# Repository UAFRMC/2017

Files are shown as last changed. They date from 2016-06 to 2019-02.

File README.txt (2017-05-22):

This is the public repo for UAF's NASA Robot Mining Contest team,
Aurora Robotics.
This is the firmware and control stack for UAF's entry in the NASA Robot Mining Competition.

Public access:
	git clone https://github.com/UAFRMC/2017

Ask Mike or Dr. Lawlor to get write access!

2017 Competition
KSCCOMM-GUEST wifi: 1632061632051282171927740A

------------- 2015 notes:
Laptop battery power check:
	cat /sys/class/power_supply/BATX/charge_*
The first two are charge values for full; the last is current charge.

As-built storage bucket dimensions:
  17.75 inch * 17 inch * 3.5 inch = 17.3 liters -> 17Kg at 1 Kg/L density (fluffed)

---------- 2014 notes:
New 2014-05 board:

Power plug:
  tx1 via opto-isolator: orange/white
  a8: orange, not connected (avoid noise on opto line)
  a9: blue, mine voltage
  a10: green, spare input
  a11: brown, 24v bus
  brown/white: motor side ground

Front plug:
  53/A15: blue, front wheel right encoder
  52: orange, (5v) encoder supply
  51: spare button input
  50/A14: green, front wheel left encoder (optional)
  White: all grounds

Back/bucket plug:
  49: orange, (5v) encoder supply
  48: orange/white, spare input
  47: green, back right button
  46/A13: blue back bucket
  45: brown/white, spare
  44: brown & blue/white, back left button 
  43: spare input

Infrared board: pink RJ45 wires
A5	A1	orange/white: read side of mining detector
   5		orange: 5V feed for ALL ir detectors (soft power for both)

A6	A2	green/white: ir detector, bin-full
3	A4	green: LED, bin-full

4	7	blue: LED, bin-half-full
A7	A3	blue/white: ir detector, bin-half-full
	
 hardwired	brown/white: LED ground (COMMON ground, hardwired)
2	6	brown: LED for mining encoder

Wiring hookup: 
mining:  brown brown/white LED    orange orange/white detector
full:	green  brown/white LED    orange green/white detector
half:   blue   brown/white LED    orange blue/white detector

Actuator Ecoder wires:
Yellow: High
White: GND
Purple: Signal

Linear actuator to RJ45 wiring:
	yellow: 5V for potentiometer position encoder, orange on RJ-45.
	white: ground for potentiometer, white/blue on RJ-45.
	purple: potentiometer output, blue or green on RJ-45.
	red: motor+, either brown (front) or separate wires (bucket)
	black: motor-, either white/brown or separate wires

# Add backend and viewer directories to path
AURORA=/home/robot/robotmining/autonomy
PATH="$AURORA/aruco/viewer:$AURORA/backend:$PATH"
export PATH

-------------
OLD 2014-03 board:

OLD: Internal voltage monitoring: 2014-03 board (OLD)
	A8: orange battery 12V bus
	A9: battery ground (drive sabertooth)
	A10: brown battery 24V bus
		Weirdly, it reads about 3VDC lower than reality, possibly due to some sort of current backfeed in the voltage divider.
		Battery sags by about 15DN under a 10A load.
	A11: battery ground (mine sabertooth)
	A12: green mining motor voltage
		Typical run voltage is 10-13DN less than battery.
		Stall voltage is 20-22DN less than battery.
		Firmware calls it "stalled" with >18DN difference.
		Swaping to a CAT5 cable, still about 10DN run, but 30+DN stall.
	
OLD: External switches:
	44- left bumper switch (brown & white/green ground)
	47- right bumper switch (green & white/green ground)

OLD: Dump actuator potentiometer hookup:
	49-orange (5V) & white/blue (gnd)
	46 - blue - analog out for dump potentiometer (jumpered to A0 for now)

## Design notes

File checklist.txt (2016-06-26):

A: away team    B: bridge

============================================================
Startup
============================================================
(A) Router Plug-in
	(B) Pilot has IP
(A) Marker Setup
(A) Align Hooks
(A) Battery Reset
(A) Arduino Cable
(A) Laptop Open
(A) Safety Off
(A) Onboard Network
	(B) SSH
	(B) Start backend
	(B) Telemetry
	(B) Drive mode
(A)//Webcam Focus
(A)//Webcam Direction
(A) Close Laptop

============================================================
End
============================================================
(A)Safety On
(A)Run "off"
(A)Wh Reading
(A)Battery Unplug
(A)Cleanup

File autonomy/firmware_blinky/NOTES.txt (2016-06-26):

Stepper + blinky receiver
2mm gap blinder black PLA
Arduino nano emitter & detector

Stepper safe zone is about 100 to 3850.

Taking individual jumps of size 100 gives a cycle time of 30 seconds (!), way too slow.  And we seem to miss IR pulses during the jump.
Taking steps of size 10 takes over a minute per cycle.

Multipath via big shiny objects like laptop screen is definitely a thing.

Overriding AccelStepper::step and adding an IR probe seems to work well.  That nest of virtual functions is not at all high performance anyway.

Blasting out one 8-bit message with a delay of 1ms is about one message every 3-4 steps.
With the wide 2mm blinder gap, message receive window seems to be about 30-40 steps, so we get about 10 messages.

Backlash is big--average received step is:
	1450-3 on downhill
	1488-90 on uphill
	Average shift is 33.8 steps, so split difference at 17 steps in each direction.
Standard deviation is 2.3 or 1.6 (down)
Worst case over 500 runs is +-5 (!).

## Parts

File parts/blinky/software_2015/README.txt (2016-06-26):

Simple infrared blinking beacon.  Blink rate is fairly slow, 4 or 5 milliseconds per cycle, to allow software signal processing.

Signal recovery is using a complex-valued "phasor" system, where we scale the incoming amplitude by a time-varying complex helix.  Frequencies that don't match the helix spin rate have low resulting amplitudes.

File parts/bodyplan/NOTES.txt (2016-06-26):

Robot driving coordinate system:
X: robot's left and right, robot right +x
Y: robot's forward and backward, robot forward +y
Z: robot's up and down, up +z

Fabrication coordinate system:
Y=0 is back of bottom steel tubing

Gearboxes:
	Diameter 9cm at output gear
	Total height 10.5cm
	axle to motor max: 10.5cm

Bottom frame:
	Y=0 is back end of tube
	Y=2.25 inch is axle pivot hole
	Y=4.75 inch is start of back drive motor mount
	Y=7.125 is start of back electronics box upright 
		21.75" tall
	Y=15.5 is centerline of ski mount
	  total of   2.875" between inner holes
	  total of   4.5" between outer holes
	  ski mount is 6 inches long

	Y=18.5 is start of up/down linear mount
		1.5" tall to pivot point
	Y=22.75 is start of front electronics box upright
	Y=25.25 is start of front drive motor mount
	Y=29.125 is front end of tube

Mining head:
	Back support is at 45 degrees to vertical in neutral configuration (linear actuators at 12" center to center)
		Back pivot to mining head is 19"
		Back pivot to linears is 20"
	Mining head is at 60 degrees to vertical in neutral
		From bottom of mount:
		Runs 5.25" up to mine drive axle
		Runs 19.25" down to mine idler axle

Linear actuators: max length 16" axle to axle

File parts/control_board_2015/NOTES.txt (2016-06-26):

Idea is the thing sits on the end of the Arduino Mega, occupying analog A8-15 (for battery & motor voltage monitoring) and the last few digital pins.

For monitoring voltages up to 24.8VDC from a 4.5V microcontroller, I need a voltage divider to ground.  I have a bunch of big 2Kohm and 348ohm surface mount resistors, which would give me up to 25.8VDC monitoring capability, while burning only 10mA of static current.  These surface mounts are only 3mm/0.11" wide, so they should be easy to fit.

2014-03-01: Milled prototype board, and soldered it up.

I needed to hack in "pinMode(p,INPUT_PULLUP)" support for Firmata (hardcoded, but seems to basically work).  Weirdly, you can't seem to digitalWrite in INPUT_PULLUP mode.

For the encoder wheel, the blue/green lines show up as digital pins 53 and 50.
The orange/brown lines should thus be digital pins 51 and 52.

It's tempting to switch the analog inputs over to RJ-45, like the digitals.

Analog via 2K:
	- Vin 132
	- Gnd 0
	- 3.3v rail 97-103 (implying total range is about 33v)
	- Aref 149-150
The Mega can call analogReference(INTERNAL1V1) for a 1.1v internally generated reference (and hence better millivolt accuracy).

-----------------------------
Version 2:

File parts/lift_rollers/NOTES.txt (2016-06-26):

Storage bag lifting rollers, with drive splines to attach to mining head crossbar.

Mining head crossbar is 1.5 inch (nom) ABS pipe OD: 48.5mm

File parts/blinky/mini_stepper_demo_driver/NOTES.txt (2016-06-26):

http://smile.amazon.com/USPRO-Stepper-28BYJ-48-4-Phase-ULN2003/dp/B00JB22IQC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

http://www.bajdi.com/joystick-and-2-28ybj-48-stepper-motors/

Each coil is about 100mA draw, for 200mA total.
64 steps per internal revolution, but it's geared way down, 
to approximately 2048 steps per output revolution.

CAD dimensions:
Output shaft:
	4.91mm dia
	2.91mm between flats
	5.9mm flat height
	8.24mm tip to boss start

Output boss:
	9.15mm diameter cylinder
	1.1mm boss height above face
	1.35mm from boss rim to body rim
	-> 8.12mm from body center to boss center

Body:
	28.1mm body diameter
	19.3mm body height
	18.1mm back wiremount width
	3.1mm back wiremount additional radius
	-> 17.15mm wiremount back radius

Mount:
	4.11mm dia mounting ear holes
	7mm dia outside ears
	41.91mm outside to outside ear
	30.81mm inside to inside ear
	-> 17.45mm body center to ear center

To find the actual steps per rev, hot glued a mirror to the output shaft, and bounced a laser off it.  There's a ton of backlash.  Every 4th half-step doesn't shift the output position.

2037 steps/rev?

Align at:
1
2038
4074
6112
8149-50
10187
12228

Dropped maxsteps from 4K to 2K:
1
2038
4080
6116

Dropped accel to 50:
1
2039
4077
6114
8149
10187
12223
(lost steps on return)

Dropped maxsteps from 2K to 1K:
1
2039
4074
6112
8150
10189
12227
(STILL loses steps on return!)

Dropped maxsteps from 1K to 600:
0
2038
4076

8156

12233
back to 0 OK.

Backlash is equivalent to about 20 steps.

http://forum.arduino.cc/index.php?topic=71964.15
Counted teeth in gearbox to get
25792/405 = 63.68395
25792/405*32 =  2037.88641975309

12227/6 =  2037.83333

http://www.airspayce.com/mikem/arduino/AccelStepper/
http://www.embedded.com/design/mcus-processors-and-socs/4006438/Generate-stepper-motor-speed-profiles-in-real-time

---------------
Plugged directly down into Arduino Uno's pins 8-11, the appropriate startup is:
AccelStepper stepper(AccelStepper::HALF4WIRE, 8,10,9,11);

Driven from 12V (lithium 3S), the stepper gets wickedly hot (approx 140F), and draws half an amp, but this works reliably:
     stepper.setMaxSpeed(3000.0);  stepper.setAcceleration(100000.0);

Driven from 8V (lithium 2S), draw is 0.3 amp, and the stepper only hits 110F (toasty).
     stepper.setMaxSpeed(3000.0);  stepper.setAcceleration(100000.0);

On a 5Ah lipo, running at 8V for an hour only drops the lipo by 0.2V (maybe 10% of full charge).

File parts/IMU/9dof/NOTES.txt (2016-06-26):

9DOF sensor board: 
https://www.sparkfun.com/products/10724

Code to pull I2C data:
http://playground.arduino.cc//Main/SEN-10724

Typical values:
A	49	-5	233	G	97	171	45	C	-24	-306	-9
A	41	-9	234	G	102	180	62	C	-24	-306	-9
A	41	-9	234	G	119	178	43	C	-24	-306	-9
A	47	-3	245	G	127	186	71	C	-24	-306	-9
A	55	-6	247	G	126	150	57	C	-24	-306	-9
A	55	-6	247	G	93	171	77	C	-24	-306	-9
A	48	-8	240	G	122	170	62	C	-24	-306	-9
A	47	-2	249	G	103	199	63	C	-24	-306	-9
A	52	-2	228	G	110	183	53	C	-24	-305	-9
A	52	-2	228	G	87	128	66	C	-24	-305	-9
A	52	3	246	G	102	170	68	C	-24	-305	-9
A	42	-17	229	G	110	178	48	C	-24	-305	-9
A	42	-17	229	G	109	186	75	C	-24	-305	-9
A	45	-7	243	G	120	175	66	C	-24	-305	-9
A	49	-4	245	G	86	167	57	C	-24	-305	-9
A	49	-4	245	G	109	174	67	C	-24	-305	-9
A	47	-1	239	G	107	155	61	C	-24	-305	-9
A	44	-3	239	G	93	168	56	C	-24	-305	-9
A	44	-3	239	G	105	196	80	C	-23	-304	-9
A	54	-2	247	G	104	152	72	C	-23	-304	-9
A	51	2	254	G	104	180	62	C	-23	-304	-9
A	51	2	254	G	73	163	48	C	-23	-304	-9
A	52	0	249	G	83	153	62	C	-23	-304	-9
A	52	-4	245	G	115	153	83	C	-23	-304	-9
A	52	-4	245	G	66	151	30	C	-23	-304	-9
A	44	-13	238	G	97	164	15	C	-23	-304	-9
A	49	-4	241	G	111	190	66	C	-23	-304	-9
A	49	-4	241	G	93	178	69	C	-23	-304	-9
A	55	-12	235	G	97	178	69	C	-23	-305	-9
A	51	0	249	G	81	155	63	C	-23	-305	-9

Accelerometer: ADXL345
Accelerometer G value shows 267 dn == 1 g.  Vector points down. 
	Datasheet rating is 4 milliG / LSB; scale factor is per chip.
Accel X axis seems the opposite of what's shown on the board, unless you flip it in software (fixed).
Accelerometer values are horribly ratty, and bounce around a ton even if you average 100.

Gryo: ITG-3200
Gyro readings seem to be relative: rates, not angles.
Gyro outputs are *very* clean, detecting even very slow rotations.
	Datasheet rating is 14 LSB per degree per second (!), up to 2000 degrees/sec.
	Datasheet sample rate is 1-8kHz.
It also reads temperature as a 16-bit quantity.
Gyro zero drift is about:
	97	60	50
Sadly, the drift slowly drifts.  The next day:
	-95.71	-114.18	42.21

Three I2C transactions results in a sample rate of about 300Hz.

Long-term averaging shows standard deviation of each reading is around 1 LSB.
1.1 1.1 1.4	1.3 1.9 1.3	0.23 0.27 0.24
Magnetometer is tighter, 0.23-0.27LSB.

Magnetometer output is funky.
We can't use a magnetometer for NASA anyway.

Same chips, better axis layout, but no magnetometer, $40:
	https://www.sparkfun.com/products/10121

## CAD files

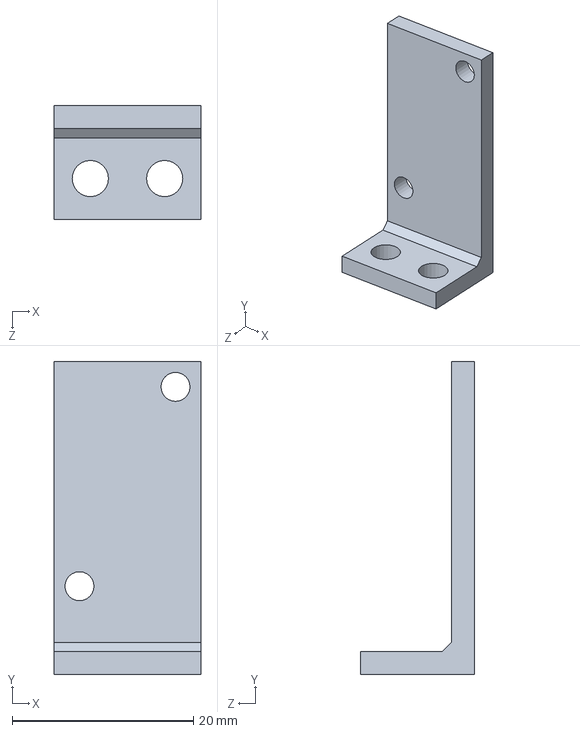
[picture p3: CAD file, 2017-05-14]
parts/limit_switches/switch_L_bracket_left.SLDPRT
16.2 x 34.5 x 12.5 mm

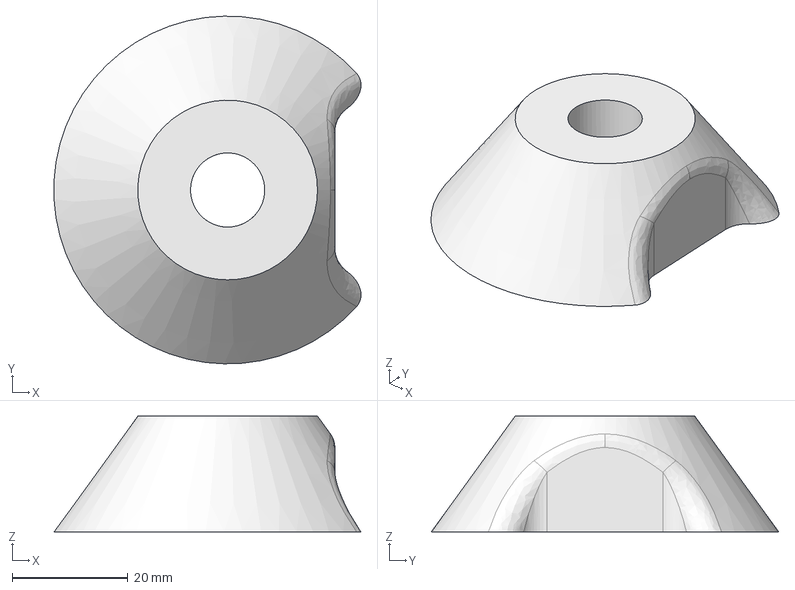
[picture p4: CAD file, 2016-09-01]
parts/mantis_2015/centercone_v2.FCStd
53.0 x 60.0 x 20.0 mm

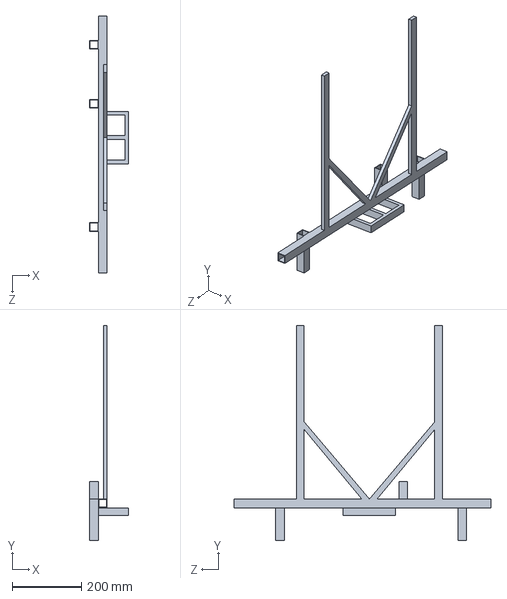
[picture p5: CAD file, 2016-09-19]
parts/Solidworks/RMC_Side.SLDPRT
112.0 x 620.0 x 740.0 mm

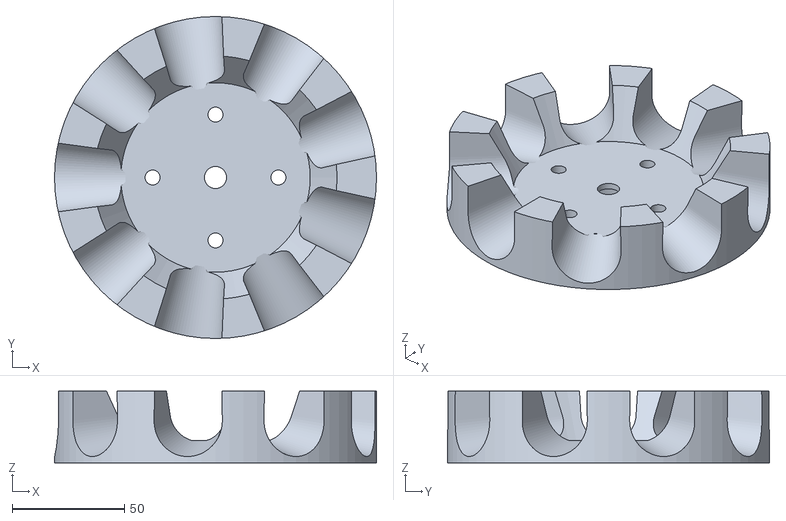
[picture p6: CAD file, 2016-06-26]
parts/tracks/drive_sprocket/2015_9tooth/Drive_Sprocket_Param.stl
143.2 x 143.2 x 32.0

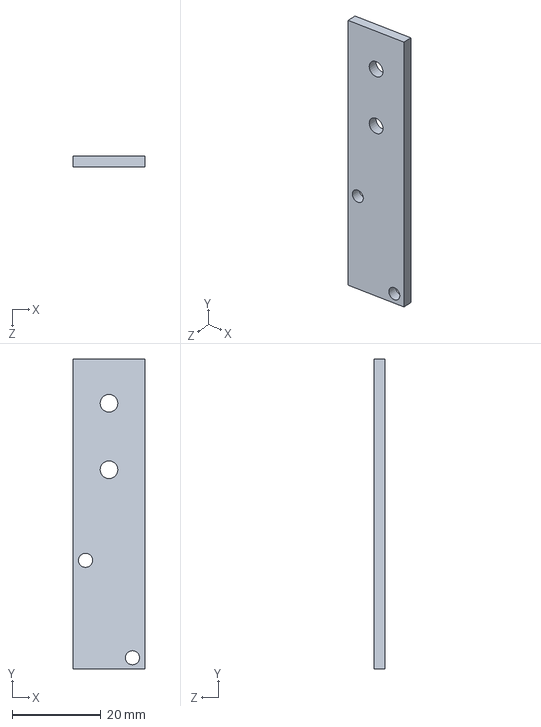
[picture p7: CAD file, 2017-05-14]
parts/limit_switches/switch_bracket_straight.SLDPRT
16.2 x 70.0 x 2.54 mm

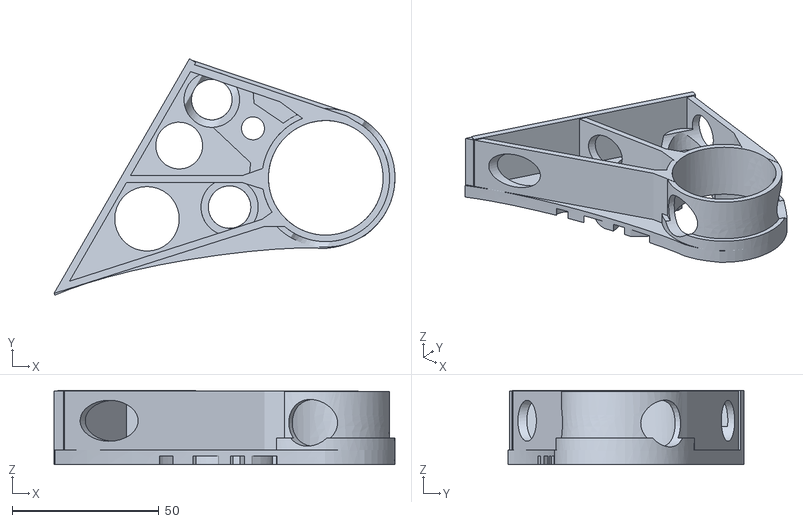
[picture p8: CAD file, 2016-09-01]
parts/mantis_2015/gearmount_v5_RIGHT.stl
116.4 x 80.7 x 25.4

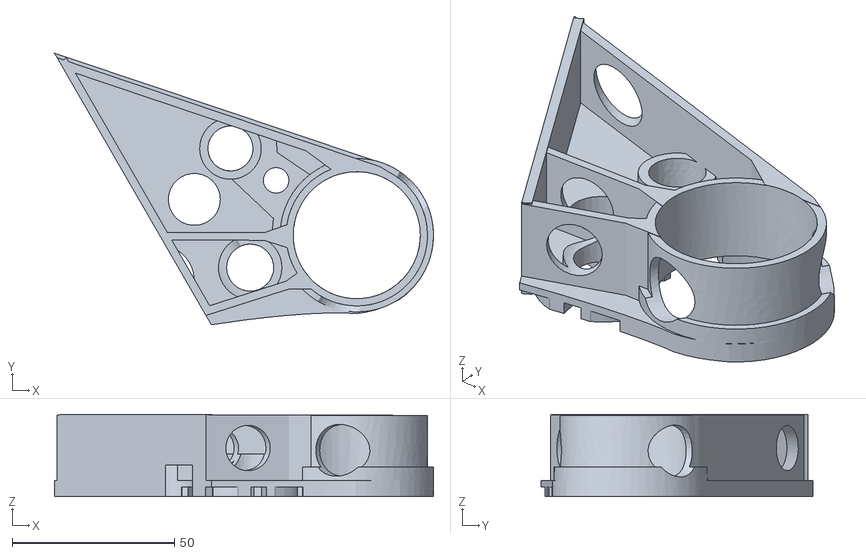
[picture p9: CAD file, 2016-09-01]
parts/mantis_2015/gearmount_v5_LEFT.stl
116.7 x 83.6 x 25.4

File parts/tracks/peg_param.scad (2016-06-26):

/*
  Track drive stud parameters.
*/
$fa=5;
$fs=0.2;

peg_IR=12; // overall peg size
peg_height=16; // overall peg height
peg_tilt=0.5; // sides sloped inward this far
peg_CR=6; // peg rounded top radius

module peg_2D_oneside() {
    translate([peg_IR-peg_tilt-peg_CR,peg_height-peg_CR,0])
        circle(r=peg_CR);
    polygon(points=[
        [0,0],
        [peg_IR,0],
        [0,peg_height]
    ]);
}

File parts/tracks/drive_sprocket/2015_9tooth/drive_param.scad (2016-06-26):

hole_num = 9; // number of holes
hole_period = 50; // Distance between centers of two consecutive holes


center_hole_diam = 3/8*25.4; // 9.525;// 3/8 inch
bearing_outer_diam = 7/8*25.4; // 22.225; // 7/8 inch
bearing_width = 9/32*25.4; // 7.14375; // 9/32 inch
mount_screw_hole = 0.25*25.4; // 6.35; // 1/4 inch

mount_screw_dis = 28; //distance between center of mounting screw hole and center
mount_hole_num = 4;

epsilon = 0.1;

wiggle= 0.3; // wiggle room for holes

$fs=0.2; // flatness tolerance (mm)
$fa=5; // angle tolerange (deg)

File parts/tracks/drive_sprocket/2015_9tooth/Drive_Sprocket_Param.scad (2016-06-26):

// Parameterizable Drive Sprocket for Robot Mining
// Ryker Dial
// October 25, 2015

include <drive_param.scad>

hole_depth = 30.5;
hole_diam_outer = 32; //37;
hole_diam_inner = 23;
teeth_top_depth = 17.5; 
base_extra = 0; // Add extra height to sprocket
sprocket_height = 32+base_extra;

hole_tilt=5; // degrees that peg holes are tilted inwards

hole_Z_center=25-hole_diam_outer/2; // Z height to center of drive sprocket


module peg_hole_trapezoid(add_width,ht) {
  hull(){
    cylinder(h=ht, d1= hole_diam_inner, d2=hole_diam_outer+add_width);
    translate([hole_depth, 0, 0])
        cylinder(h=ht, d1= hole_diam_inner, d2=hole_diam_outer+add_width);
  }
}


module sprocket(){
    sprocket_circum = hole_num*hole_period;
    sprocket_radius = sprocket_circum/(2*PI);
    difference(){
   // minkowski(){
    difference(){
        cylinder(r=sprocket_radius, h=sprocket_height);
        // Remove center material
        translate([0,0,10+epsilon]){
            cylinder(r1=sprocket_radius-hole_depth+10*epsilon, r2=sprocket_radius-teeth_top_depth, h=sprocket_height-10);
        }
        // Peg holes
        translate([0,0,hole_Z_center]){
            for(i=[0:hole_num-1]){
                translate([0,0,hole_diam_outer/2]){
                    rotate([0,270-hole_tilt,i*360/hole_num]){
                        translate([0,0,sprocket_radius-hole_depth]){
                            peg_hole_trapezoid(0,hole_depth+3);
                            translate([0,0,hole_depth-7])
                              rotate([0,hole_tilt,0])
                                peg_hole_trapezoid(10,10);
                        }
                    }
                }
            }
        }
    }
   // sphere(1);
//}
        // Center hole
        translate([0,0,-(epsilon+1)]){
            cylinder(d=center_hole_diam+wiggle, h=sprocket_height);
        }
        // Hole for bearing
        translate([0, 0, -(epsilon+1)]){
            cylinder(d=bearing_outer_diam+wiggle, h=bearing_width+wiggle+1);
        }

        // Mounting Holes
        for(i=[0:mount_hole_num-1]){
            rotate([0,0,i*360/mount_hole_num]){
                translate([0, mount_screw_dis, -(epsilon+1)]){
                    cylinder(d=mount_screw_hole+wiggle, h=sprocket_height);
                }
            }
        }
 //   }
    }
}

sprocket();

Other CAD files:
parts/limit_switches/switch_L_bracket_right.SLDPRT
parts/mining_head/drive_sprocket.scad
parts/bag_winder/bag_winder.scad
parts/bag_winder/drive_param.scad
parts/bag_winder/roundlib.scad
parts/gearbox/gearbox.scad
parts/lift_rollers/splines.scad
parts/limit_switches/switch_L_bracket_left.STL
parts/limit_switches/switch_L_bracket_right.STL
parts/limit_switches/switch_bracket_straight.STL
parts/mantis_2015/centercone_v2.iges
parts/mantis_2015/centercone_v2.stl
parts/mining_head/barbie_gearbox.scad
parts/mining_head/scoop_sides/scoopsi.scad
parts/motors/motor_cap.scad
parts/power_rails/RMC_power_rail_cap.scad
parts/tracks/boat_prow/boat_prow.scad
parts/tracks/drive_pegs.scad
parts/tracks/drive_sprocket/2015_5tooth/double_drive_sprocket.scad
parts/tracks/drive_sprocket/2015_5tooth/drive_sprocket.scad
parts/tracks/drive_sprocket/2015_9tooth/mount.scad
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

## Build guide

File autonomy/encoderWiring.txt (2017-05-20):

2017 encoder bus (from firmware, should all be working)

Bus 1: roll motor and limit switches

pin 3, Arduino 48, Limit switch, top
pin 4, Arduino 34, 
pin 5, Arduino 50, Limit switch, bottom
pin 6, Arduino 32, Roll motor
pin 7, Arduino 52, 
pin 8, Arduino 30, 

Bus 2: mining and drive wheels

pin 3, Arduino 42, Mining head
pin 4, Arduino 40, Right front wheel
pin 5, Arduino 44, Left front wheel
pin 6, Arduino 38, 
pin 7, Arduino 46, Right back wheel
pin 8, Arduino 36, Left back wheel

OBSOLETE 2016 encoder bus:
Motor 	Encoder#	Analog Pin
DR1		4	  		A1
DR2		8			A5
DL1		5			A2
DL2		7			A4
M 		3			A0
R		6			A3

Notes:DR1 is the left side front drive motor. This convention follows for all drive motors

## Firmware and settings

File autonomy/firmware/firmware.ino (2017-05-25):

/**
 * Aurora Robotics "Autonomy" firmware - 2015 BTS Version
 * For Arduino Mega
 */
#include "robot.h" /* classes shared with PC, and across network */
#include "serial_packet.h" /* CYBER-Alaska packetized serial comms */
#include "encoder.h"
#include "milli.h"
#include "pid.h"
#include "bts_motor.h"
#include "speed_controller.h"

/* Subtle: I don't need a namespace, but this at least disables the Arduino IDE's
utterly broken prototype generation code in the Arduino IDE. */
namespace aurora {

int bts_enable_pin=22;
// Hardware pin wiring (for Mega)
BTS_motor_t motor_M(10,11,200);
BTS_motor_t motor_D(12,3,255); //Bag rolling motor
BTS_motor_t motor_L(8,9,60);
BTS_motor_t motor_R(4,5,60);
BTS_motor_t motor_F(6,7,255);

// Call this function frequently--it's for minimum-latency operations
void low_latency_ops();

/** This class manages communication via an A_packet_formatter,
 including timeouts. */
class CommunicationChannel {
public:
  HardwareSerial &backend;
  A_packet_formatter<HardwareSerial> pkt; // packet formatter
  bool is_connected; // 1 if we're recently connected; 0 if no response
  milli_t last_read; // millis() the last time we got data back
  milli_t next_send; // millis() the next time we should send off data

  CommunicationChannel(HardwareSerial &new_backend) :
  backend(new_backend), pkt(backend)
  {
    is_connected=0;
    last_read=milli;
    next_send=milli;
  }

  bool read_packet(A_packet &p) {
    p.valid=0;
    if (backend.available()) {
      while (-1==pkt.read_packet(p)) {
        low_latency_ops(); /* while reading packet */
      }
      if (p.valid && p.length>0) {
        last_read=milli;
        next_send=milli;
        is_connected=true; // got valid packet
        //digitalWrite(13,HIGH); // !!(milli&(1<<8))); // blink while getting good data
        return true;
      }
    }
    if (milli-next_send>500) { // read timeout
      next_send=milli;
      pkt.reset();
      pkt.write_packet(0,0,0); // send heartbeat ping packet
      is_connected=false;

      //digitalWrite(13,0); // LED off if disconnected
    }
    return false;
  }
};

// All PC commands go via this (onboard USB) port
HardwareSerial &PCport=Serial; // direct PC
HardwareSerial &BlinkyLport=Serial1; // serial comms to blinky nanos
HardwareSerial &BlinkyRport=Serial2; // serial comms to blinky nanos

CommunicationChannel PC(PCport);
CommunicationChannel BlinkyL(BlinkyLport);
CommunicationChannel BlinkyR(BlinkyRport);

const int encoder_raw_pin_count=12;
const int encoder_raw_pins[encoder_raw_pin_count]={48,34,50,32,52,30, 42,40,44,38,46,36};

const int encoder_bus_1[9]={0,0,0, 48,34,50,32,52,30}; //bus 1-4
const int encoder_bus_2[9]={0,0,0, 42,40,44,38,46,36}; //bus 5-8

enum
{
  NUM_AVERAGES=2
};
speed_controller_t<NUM_AVERAGES> encoder_M(4,0,0,encoder_bus_2[3],80,motor_M); // Mining head left side motor
speed_controller_t<NUM_AVERAGES> encoder_R(4,0,0,encoder_bus_1[6],80,motor_D); // Encoder for roll motor
speed_controller_t<NUM_AVERAGES> encoder_DL1(4,0,0,encoder_bus_2[5],13,motor_L);  //Left front wheel encoder
speed_controller_t<NUM_AVERAGES> encoder_DL2(4,0,0,encoder_bus_2[8],13,motor_L);  //Left back wheel encoder
speed_controller_t<NUM_AVERAGES> encoder_DR1(4,0,0,encoder_bus_2[4],13,motor_R); //Right front wheel encoder
speed_controller_t<NUM_AVERAGES> encoder_DR2(4,0,0,encoder_bus_2[7],13,motor_R);  //Right back wheel encoder

encoder_t limit_top(encoder_bus_1[3]);
encoder_t limit_bottom(encoder_bus_1[5]);





/***************** Robot Control Logic ****************/

long mine_last=0; // millis() at last mining motion check
long stall_last=0; // timer for stall detection average
int sum_stalled=0, sum_stall_count=0;


// Robot's current state:
robot_current robot;

// Read all robot sensors into robot.sensor
void read_sensors(void) {
  robot.sensor.battery=0; 
  low_latency_ops();

  robot.sensor.Mstall=encoder_M.stalled;
  robot.sensor.DRstall=encoder_DL1.stalled;
  robot.sensor.DLstall=encoder_DR1.stalled;
  robot.sensor.limit_top=limit_top.count_mono;
  robot.sensor.limit_bottom=limit_bottom.count_mono;
  ++robot.sensor.heartbeat;
  
  
  robot.sensor.encoder_raw=0;
  for(int ii=0;ii<encoder_raw_pin_count;++ii)
    robot.sensor.encoder_raw|=digitalRead(encoder_raw_pins[ii])<<ii;
}


void set_direction(int power64, encoder_t &enc)
{
  //Update encoder direction
  if (power64>64) enc.last_dir=+1;
  if (power64<64) enc.last_dir=-1;

}
// Match up motor power value with encoder
void send_motor_power(int power64,BTS_motor_t &motor,encoder_t &enc) {
	// update encoder direction
	set_direction(power64,enc);
	// send to motor
  motor.drive(power64);
}

// Send current power values to the motors
void send_motors(void)
{
  if(robot.power.motorControllerReset!=0)
    digitalWrite(bts_enable_pin,LOW);
  else
    digitalWrite(bts_enable_pin,HIGH);
 
  int drivePower=255;
/*  int drivePower=100;
  if(robot.power.high)
  {
    drivePower=255;
  }*/
  motor_L.max_power=drivePower;
  motor_R.max_power=drivePower;
  
  int left1=encoder_DL1.update(robot.power.left,robot.power.torqueControl==0);
  send_motor_power(left1,motor_L,encoder_DL1);
  set_direction(left1,encoder_DL2);

  int right1=encoder_DR1.update(robot.power.right,robot.power.torqueControl==0);
  send_motor_power(right1,motor_R,encoder_DR1);
  set_direction(right1,encoder_DR2);


  int roll = encoder_R.update(robot.power.roll,robot.power.torqueControl==0, 6);
  send_motor_power(robot.power.roll,motor_D,encoder_R);

  // automated mining at fixed rate
  int mine=robot.power.mine;
  //mine=encoder_M.update(mine,robot.power.mineMode!=0||robot.power.mineDump!=0);
  mine=encoder_M.update(mine,robot.power.torqueControl==0,24);
  send_motor_power(mine,motor_M,encoder_M);

  motor_F.drive(robot.power.dump);
}

// Structured communication with PC:
void handle_packet(A_packet_formatter<HardwareSerial> &pkt,const A_packet &p)
{
  if (p.command==0x7) { // motor power commands
    low_latency_ops();
    if (!p.get(robot.power)) { // error
      pkt.write_packet(0xE,0,0);
    }
    else
    { // got power request successfully: read and send sensors
      low_latency_ops(); /* while reading sensors */
      read_sensors();
      low_latency_ops();
      pkt.write_packet(0x3,sizeof(robot.sensor),&robot.sensor);
      robot.sensor.latency=0; // reset latency metric
      low_latency_ops();
    }
  }
  else if (p.command==0) { // ping request
    pkt.write_packet(0,p.length,p.data); // ping reply
  }
}

/**** Low latency (sub-millisecond) timing section.
 * We need this for maximum accuracy in our encoder counts.
 */

milli_t last_milli=0;
void low_latency_ops() {
  unsigned long micro=micros();
  milli=micro>>10; // approximately == milliseconds

  

  //Encoder for mining motor
  encoder_M.read();
  // robot.sensor.Mspeed=encoder_M.period;
  robot.sensor.Mcount=encoder_M.count_mono;

  //Encoder for roll motor
  encoder_R.read();
  robot.sensor.Rcount=encoder_R.count_dir;


  //Encoder stuff for left drive track
  encoder_DL1.read();
  robot.sensor.DL1count=encoder_DL1.count_dir;

  encoder_DL2.read();
  robot.sensor.DL2count=encoder_DL2.count_dir;

  //Encoder stuff for right drive track
  encoder_DR1.read();
  robot.sensor.DR1count=encoder_DR1.count_dir;

  encoder_DR2.read();
  robot.sensor.DR2count=encoder_DR2.count_dir;
  
  limit_top.read();
  limit_bottom.read();

  // Update latency counter
  unsigned int latency=milli-last_milli;
  if (latency>=1024) latency=1023;
  if (robot.sensor.latency<latency) robot.sensor.latency=latency;
  last_milli=milli;
}


}; // end namespace aurora


void setup()
{
  aurora::PCport.begin(57600); // Control connection to PC via USB

  // Our ONE debug LED!
  //pinMode(13,OUTPUT);
  //digitalWrite(13,LOW);

  // BTS Enable Pin (Controls all pins)
  pinMode(aurora::bts_enable_pin,OUTPUT);
  digitalWrite(aurora::bts_enable_pin,HIGH);

}


milli_t milli;
milli_t next_milli_send=0;
void loop()
{
  aurora::low_latency_ops();

  A_packet p;
  if (aurora::PC.read_packet(p)) aurora::handle_packet(aurora::PC.pkt,p);
  if (!(aurora::PC.is_connected)) aurora::robot.power.stop(); // disconnected?

  if (milli-next_milli_send>=5)
  { // Send commands to motors
    aurora::send_motors();
    next_milli_send=milli; // send_motors every 5ms
  }
}

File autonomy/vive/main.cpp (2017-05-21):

//Data recorder mod with GUI showing light positions.
/*
 Modded by OSL 2017-04-16 to try to figure out calibration for RMC configuration:
  Emitters facing in the same direction, 1.5 meters apart.
 

*/
#include <stdio.h>
#include <stdlib.h>
#include <stdint.h>
#include <survive.h>
#include <string.h>
#include <os_generic.h>

#include "osl/file_ipc.h"
#include "osl/transform.h"
#include <vector>

#include "src/survive_cal.h"
#include <CNFGFunctions.h>
#ifdef __unix__
#include <unistd.h>
#endif

#include "src/survive_config.h"


/**
  Return the current time in seconds (since something or other).
*/
#if defined(_WIN32)
#  include <sys/timeb.h>
#  define time_in_seconds_granularity 0.1 /* seconds */
double time_in_seconds(void) { /* This seems to give terrible resolution (60ms!) */
        struct _timeb t;
        _ftime(&t);
        return t.millitm*1.0e-3+t.time*1.0;
}
#else /* UNIX or other system */
#  include <sys/time.h> //For gettimeofday time implementation
#  define time_in_seconds_granularity 0.01 /* seconds */
double time_in_seconds(void) {
	struct timeval tv;
	gettimeofday(&tv,NULL);
	return tv.tv_usec*1.0e-6+tv.tv_sec*1.0;
}
#endif

#include "osl/vec4.h"



void survive_vec3_print(const char *heading, vec3 v)
{
  printf("%s: ( %.5f %.5f %.5f )\n", heading, v[0], v[1], v[2]);
}



/* A coordinate frame made from three unit vectors */
typedef struct SurviveObjectOrientation {
  // Orientation matrix (orthogonal unit vectors)
  vec3 x,y,z;
  
} SurviveObjectOrientation;

// Initialize this orientation to the identity
void survive_orient_init(SurviveObjectOrientation *o) {
  o->x=vec3(1,0,0);
  o->y=vec3(0,1,0);
  o->z=vec3(0,0,1);
}

void survive_orient_print(SurviveObjectOrientation *o) {
  survive_vec3_print("   X",o->x);
  survive_vec3_print("   Y",o->y);
  survive_vec3_print("   Z",o->z);
}

// Convert local coordinates out into global coordinates
vec3 survive_orient_global_from_local(SurviveObjectOrientation *o, vec3 local)
{
  return local.x*o->x + local.y*o->y + local.z*o->z;
}

// Convert global coordinates down into local coordinates
vec3 survive_orient_local_from_global(SurviveObjectOrientation *o, vec3 global)
{
  return vec3(dot(global,o->x), dot(global,o->y), dot(global,o->z));
}


// Apply these incremental rotation angles to this orientation
//    angle.x rotates about the x axis, etc.
//    angle vector is in local coordinates, radians, and right handed
void survive_orient_rotate(SurviveObjectOrientation *o, vec3 angle)
{
  o->z+= angle.y*o->x - angle.x*o->y;
  o->y+=-angle.z*o->x;
	o->x=normalize(cross(o->y,o->z));
	o->y=normalize(cross(o->z,o->x));
	o->z=normalize(o->z);
}

// Nudge our coordinate frame to make these two vectors equal:
//    local_measured (local coordinates) is what it's reading
//    global_should is what it should read
//    strength is how fast it should get there (0-1)
void survive_orient_nudge(SurviveObjectOrientation *o, vec3 local_measured, vec3 global_should, FLT strength)
{
  local_measured=normalize(local_measured);
  vec3 local_should=normalize(survive_orient_local_from_global(o,global_should));
  vec3 shift=strength*(local_measured-local_should); // rotation force
  float max_shift=0.2; // maximum radian rotation to ever apply
  if (length(shift)>max_shift) shift=max_shift*normalize(shift);
  vec3 rotate=cross(shift,normalize(local_measured)); // torque vector
  
  // Rotate to apply that torque
  survive_orient_rotate(o,rotate);
}



/* The hardware configuration of a tracked sensor */
typedef struct SurviveSensorHardware {
  // The sensor's position, relative to the IMU
  vec3 position; 
  
  // The sensor's facing normal vector
  vec3 normal;
} SurviveSensorHardware;

/* Keeps track of the simulated position of the sensor */
typedef struct SurviveSensorTracker {
  
  // Angle, in radians, of last detection by this lighthouse.
  //   These are re-zeroed every integration step.
  double angle[NUM_LIGHTHOUSES][2];
  
} SurviveSensorTracker;

/* Simulates position of a tracked object */
typedef struct SurviveObjectSimulation {
  // time_in_seconds at our last integration step.  
  //    Used to compute timesteps.
  double last_integrate_time;
  
  // Position of the lighthouses in global coordinates
  //    FIXME: for multi-object tracking, this needs to be a shared pointer.
  vec3 lighthouse_position[NUM_LIGHTHOUSES];
  
  // Orientation of the lighthouses in global coordinates
  //    FIXME: for multi-object tracking, this needs to be a shared pointer.
  SurviveObjectOrientation lighthouse_orient[NUM_LIGHTHOUSES];
  
  // Position of our center in global coordinates (meters)
  vec3 position;
  
  // Velocity of our center in global coordinates (m/s)
  vec3 velocity;
  
  // Our orientation in global coordinates (orient.x points along our X axis)
  SurviveObjectOrientation orient;
  // IMU timesteps are faster:
  double last_imu_time;
  
  // Down vector, measured in local orient frame
  vec3 down;

  // Number of sensors actually present in these arrays:
  int nsensor;
  
  // Static info about the sensor hardware  
  const SurviveSensorHardware *hardware;
  
  // Dynamic tracking info for each sensor
  SurviveSensorTracker sensor[SENSORS_PER_OBJECT];
  
} SurviveObjectSimulation;


SurviveObjectSimulation *survive_sim_init(const char *type) {
  double now=time_in_seconds();
  SurviveObjectSimulation *o=(SurviveObjectSimulation *)malloc(sizeof(SurviveObjectSimulation));
  
  o->last_integrate_time=now;
  
  // HACK: hardcode lighthouse positions for robot setup.
  o->lighthouse_position[0]=vec3(0,0,0);
  o->lighthouse_position[1]=vec3(1.5,0,0);
  survive_orient_init(&o->lighthouse_orient[0]);
  survive_orient_init(&o->lighthouse_orient[1]);
  
  o->position=vec3(1.0,1.0,0);
  o->velocity=vec3(0,0,0);
  survive_orient_init(&o->orient);
  // flip initial estimate upside down, since controller Z+ is world Z-
  o->orient.z*=-1.0; o->orient.y*=-1.0;
  
  o->last_imu_time=now;
  o->down=vec3(0,0,0);
  
  const static SurviveSensorHardware hardware[]={
#include "survive_models/controller_cal.h"
  };
  o->hardware=hardware;
  
  // Zero out the sensors:
  for (int S=0;S<SENSORS_PER_OBJECT;S++)
    for (int L=0;L<NUM_LIGHTHOUSES;L++)
      for (int A=0;A<2;A++)
        o->sensor[S].angle[L][A]=0.0;
  
  return o;
}

// Return the global coordinates normal of the plane swept by
//   lighthouse L's axis A at angle ang radians.
vec3 survive_lighthouse_normal(SurviveObjectSimulation *o,int L,int A,FLT ang)
{
  vec3 N;
  FLT s=sin(ang), c=cos(ang);
  if (A==0) { // Sweeping across X axis
    N=vec3(-c,-s,0.0);
  } else { // Y axis sweep
    N=vec3(0.0,-s,c);
  }
  return survive_orient_global_from_local(&o->lighthouse_orient[L],N);
}
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

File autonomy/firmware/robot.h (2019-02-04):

/**
 Aurora Robotics general robot code.

 This is shared between the Arduino and the PC.

  Orion Sky Lawlor, lawlor@alaska.edu, 2014-03-23 (Public Domain)
*/
#ifndef __AURORA_ROBOTICS__ROBOT_H
#define __AURORA_ROBOTICS__ROBOT_H
#include <stdint.h> /* for uint32_t */


/**
  These are the field dimensions, in centimeters.
  Y runs up the field, from collection bin to mining area.  It's always positive.
  X runs across the field, from left to right side.  It's signed.
*/
enum {
	field_y_size=738, // Y-length of field, in centimeters
//	field_y_size=500, // Y-length of field, in centimeters for the test arena
	field_y_start_zone=183, // y end of start area, in centimeters
	field_y_mine_zone=field_y_start_zone+294, // y start of mining area
	field_y_xmit=-47, // y coordinate of IR transmitters behind bin
	field_x_xmit=70, // x coordinate between IR transmitters
//	field_y_mine_zone=field_y_start_zone+100, // y start of mining area for the test arena

	field_x_size=378, // X-width of field, in centimeters
	field_x_hsize=field_x_size/2,
	field_x_GUI=field_x_hsize+10, // start X for GUI display
	field_x_bin=156, // X-width of collection bin, in centimeters
	field_x_hbin=field_x_bin/2
};

enum {
	robot_rt_blinky=55, // robot centerline to blinky receiver center, right() direction
	robot_fw_blinky=-33 // robot centerline to blinky receiver center, forward() direction
};

enum {
/*
		DN 949 fully up
		DN 330 mining head will drag on bar
		DN 260 mining starts on level ground
		DN 240 conservative mining depth
		DN 180 fully down
*/
		head_mine_stop=250, // stop lowering at this mining height
		head_mine_start=310, // start mining at this height
		head_mine_drive=500, // normal driving height
		head_drive_safe=800, // can safely drive below this height (without tipping over)
		head_mine_dump=890, // dumping height
		head_mine_stow = 250, // stow height, where frame is level
		head_bar_clear=320, //mining head will not drag on bar
		// These 2 are used for speed control while aligning and releasing hooks
		count_stop = 1, // encoder count to stop on
		count_slow = 110, // run fast until you're here
	// These 2 are used to tell whether the box is at max or min height
	box_raise_max = 268,
	box_raise_min = 0
	};
/**
  This is a list of possible robot states.
  It's mostly maintained on the backend, but
  can be commanded from the front end.
*/
typedef enum {
	state_STOP=0, ///< EMERGENCY STOP (no motion)
	state_drive, ///< normal manual driving
	state_backend_driver, ///< drive from backend UI

	state_autonomy, ///< full autonomy start state
	state_raise, ///< raise conveyor before driving
	state_find_camera, ///< turn until camera is visible
	state_align_turnout, ///< autonomous: pivot to face start position
	state_align_drive, ///< autonomous: initial drive to start position
	state_align_turnin, ///< autonomous: turn to face lunabin
	state_align_back, ///< autonomous: drive back to contact lunabin

	state_drive_to_mine, ///< autonomous: drive to mining area

	/* Semiauto mine mode entry point: */
	state_mine_lower, ///< mining mode: lowering head, driving forward
	state_mine_stall, ///< mining mode: raising head (after stall)
	state_mine, // actually mine
	state_mine_raise, ///< existing mining mode: raise bucket

	state_drive_to_dump, ///< drive back to bin

	/* Semiauto dump mode entry point: */
	state_dump_contact, ///< final dock-and-dump mode: drive to contact bin
	state_dump_raise, ///< raising bucket
	state_dump_pull, ///< pull box up
	state_dump_rattle, ///< rattle mode to empty bucket
	state_dump_push, ///< push box back down
	state_dump_lower, ///< lowering bucket (after dump)

	/* Semiauto dump mode entry point: */
	state_stow, // begin stowing: raise bucket
	state_stow_clean, // clean bucket
	state_stowed, // finished stowing (wait forever)

	state_last ///< end state (repeat from mine_drive)
} robot_state_t;
const char *state_to_string(robot_state_t state);


/// This bitfield convey's the robot's software status.
class robot_status_bits {
public:
	unsigned char stop:1; ///< EMERGENCY STOP engaged
	unsigned char arduino:1; ///< arduino is connected correctly
	unsigned char located:1; ///< robot thinks it knows where it is
	unsigned char autonomy:1; ///< full-autonomy mode is engaged
	unsigned char semiauto:1; ///< semiauto mode is engaged
};

/** This is the Arduino's AREF analog reference voltage.
  It's the scale factor that gives true voltage output,
  and should be measured from the AREF pin against Arduino ground. */
#define AD_AREF_voltage (4.78)

/** This scale factor converts an
	Arduino Analog/Digital Data Number (0-1023)
	to a real voltage, assuming direct feed-in. */
#define AD_DN2low_voltage (AD_AREF_voltage/(1024.0))

/** This scale factor converts an
	Arduino Analog/Digital Data Number (0-1023)
	to a real voltage, after the resistor divider scaling.
*/
#define AD_DN2high_voltage ((AD_AREF_voltage)*(11.0)/1024.0)


/** This class contains all the robot's sensors, on Arduino, backend, or front end.
Raw sensor values go as bitfields, because many of them are 10-bit quantities:
	- Arduino A/D values are 10 bits each
	- Arena positions in cm are 9-10 bits each (arena is 378x738cm)
	- Blinky angle reports are about 9 bits each (500 samples per rotation)
*/
class robot_sensors_arduino
{
public:
	uint32_t battery:10; // raw A/D reading at top of battery stack (voltage = this*5*2000/384)
	uint32_t bucket:10; // raw A/D value from dump bucket lift encoder
	uint32_t latency:5; // Arduino control loop latency

	uint32_t Mstall:1;
	uint32_t DLstall:1;
	uint32_t DRstall:1;

	uint32_t stop:1; ///< EMERGENCY STOP button engaged
  	uint32_t heartbeat:3;

	uint32_t Mspeed:8; /// Current milliseconds per encoder tick for mining head left motor (255==stopped)
	uint32_t Mcount:8; /// Encoder tick count for mining head left motor

	uint32_t DL1count:8; /// Encoder tick count for front left drive wheel
	uint32_t DL2count:8; /// Encoder tick count for back left drive wheel
	uint32_t DR1count:8; /// Encoder tick count for right drive wheel
	uint32_t DR2count:8; /// Encoder tick count for back right drive wheel

	int32_t Rcount:16; /// Encoder tick for bag roll motor

  	uint32_t limit_top:8;
  	uint32_t limit_bottom:8;
  
  	uint32_t encoder_raw:16;
};


/** This class contains robot localization information. */
class robot_localization {
public:
// Raw camera-derived robot location (cm)
	float x,y,z;

// Robot's orientation relative to lunabin (degrees from lunabin)
//   angle==0 means facing directly away from lunabin (world +y = robot forward)
//   angle==90 means facing due right (world +x = robot forward)
	float angle;

// Mining head's vertical pitch, in degrees.
//    pitch==0 means the mining head is in rest configuration.
//    positive pitch pushes the mining head back up away from the ground
  float pitch;

// Confidence in our position (1.0: recent detection; 0.0: no idea)
	float confidence;
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

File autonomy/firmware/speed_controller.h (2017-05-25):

#ifndef SPEED_CONTROLLER_H
#define SPEED_CONTROLLER_H

#include <Arduino.h>
#include "encoder.h"
#include "bts_motor.h"

template<uint8_t AVERAGES> class speed_controller_t:public encoder_t
{
public:
  BTS_motor_t& motor;
  pid_t<int16_t> pid;
  milli_t last_print;
  milli_t last_power;
  milli_t times[AVERAGES];
  uint8_t times_ptr; // index into times array
  int16_t average_without_div; // average of times array
  milli_t target_time; // motor target period (ms)
  int last_dir;
  bool stalled;
  boolean backwards; // running in reverse

  speed_controller_t(const float pgain,const float igain,const float dgain,const int encoder_pin,int encoder_threshold,BTS_motor_t& motor):
    encoder_t(encoder_pin),motor(motor),pid(0,0,0),average_without_div(0),times_ptr(0),target_time(1000)
  {
    memset(times,0,sizeof(times));
    stalled=false;
    backwards=false;
    last_dir=0;
    last_print=last_power=0;
  }

  virtual void change()
  {
    times[times_ptr++]=period;
    if(times_ptr>=AVERAGES)
      times_ptr=0;

    average_without_div=0;
    for(int16_t ii=0;ii<AVERAGES;++ii)
      average_without_div+=times[ii];

    stalled=false; // evidently we're spinning!
  }

  // Update state for new commanded direction
  void set_dir(int dir) {
      backwards=dir<0;
      if (dir!=last_dir) {
        last_dir=dir;
        last_change=milli; // update timing for start of new command
      }
  }


  //target is either target pwm speed in speed control mode (when torque_control is false)
  //target is either target ms time in torque control mode (when torque_control is true)
  int update(int target,const bool speed_control,int rpm_scaler=12)
  {
    //speed control, return
    if(!speed_control) {
      last_change=milli;
      return target;
    }
    // target == 1 full reverse .. 64 stop .. 127 full forward

    //backwards calculation
    if(target<62) {
      set_dir(-1);
    }
    else if (target>=62 && target<65) {
      set_dir(0);
      stalled=false; //No power,clear stall
      return 64;
    }
    else { // target > 64
      set_dir(+1);
      target=128-target;
    }
   // target == 63 (stop) .. 0 (full power)

    //Change pwm speed to time in ms
    int rpm=(63-target)*rpm_scaler;
    if(rpm==0)
      rpm=1;
    target_time=2000/rpm;

    int min_time=2;
    int max_time=500;

    if(target_time>max_time)
      target_time=max_time;
    if(target_time<min_time)
      target_time=min_time;

    const int motor_min=68; // don't give less power than this (keep spinning)
    const int motor_max=127; // don't give more than this
    const int motor_stop=64;
    const int motor_idle=72;
    const int motor_kickstart_gentle=80;
    const int motor_kickstart_full=motor_max;
    int32_t motor_value=64;
    milli_t since_last=milli-last_change;

    if(last_power>last_change+500)
    {
       stalled=true;
    }
    
    
    {
      milli_t real_average=average_without_div;
      int count=AVERAGES;

      if(since_last>real_average/AVERAGES) // next tick is late--include it
      {
        real_average+=since_last;
        ++count;
      }

      real_average=real_average/count;

      int32_t err=((int32_t)real_average-(int32_t)target_time)*16/target_time;
      motor_value=err+motor_idle;

      // avoid spinning too slow
      if(motor_value<motor_min)
        motor_value=motor_min;
    }

    // avoid spinning too fast
    if(motor_value>motor_max)
      motor_value=motor_max;

// Debug prints
/*
    if(milli-last_print>=100)
    {
      Serial.print("MINE: ");
      Serial.print(average_without_div/AVERAGES);
      Serial.print("\t");
      Serial.println(motor_value);

      last_print=milli;
    }
*/

    if(motor_value!=64)
      last_power=milli;

    if(backwards) //running in reverse
      return (128-motor_value);
    else
      return motor_value;
  }
};

#endif

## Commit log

2016-06-26 First commit.
    [Drive_Sprocket_Param.scad, Drive_Sprocket_Param.stl, RMC_power_rail_cap.scad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]
2016-08-01 Added SCAD for track grousers.
    [grouser.scad]
2016-09-01 Added mantis parts: centercone goes inside wheels, gearmount holds the gearbox.
    [centercone_v2.FCStd, centercone_v2.iges, centercone_v2.stl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]
2016-09-19 Initial ROS commit, and upload solidworks part
    [RMC_Side.SLDPRT]
2016-09-20 Tested serial comms, automatically finds arduino.
2016-11-28 Added chain drive library.
    [barbie_gearbox.scad, drive_sprocket_chain.scad, drive_sprocket_chain_slice.scad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]
2017-02-19 Added bag wind-up adapter: gearbox on left, EMT wind-up on right.
    [bag_winder.scad, drive_param.scad, roundlib.scad]
2017-02-27 Added quick firmware to test encoder RJ-45 breakout on Bryant's main board
2017-04-12 Add obstacle avoidance, including distance to the robot parts. Should even work for an L shaped robot, although it might need a minus sign somewhere.
    [main.cpp]
2017-05-07 Don't blink pin 13, since it's hooked to motor stuff on new shields.
2017-05-10 Changed pins to the new bryant board.
2017-05-12 Brackets for limit switches
    [switch_L_bracket_left.SLDPRT, switch_L_bracket_left.STL, switch_L_bracket_right.SLDPRT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]
2017-05-14 limit switches and raw encoders
2017-05-15 Added actual limit switch detection.
2017-05-16 Added Arduino heartbeat. Cleaned up old debug in ui
2017-05-16 Added stall detection
2017-05-17 Updated coordinate system transform for vive to real measured robot and sensor center points.
2017-05-17 Kinect now works with Vive! The 3D coordinate system is transferred via file_ipc's sensor.tf, so the kinect data is put into world 3D coordinates from the vive.
2017-05-17 Initial grid-based navigation data converted from Kinect imagery. Still doesn't hook up to driving subsystem, but it does basically work, and it includes a debug utility ipc/dump_grid
    [main.cpp]
2017-05-17 Skip over spurious obstacles caused by missing data or edge pixels.
    [main.cpp]
2017-05-17 Stop mining when stall detected
    [speed_controller.h, ui.h]
2017-05-17 Added ability to reset all BTS's
    [firmware.ino, robot.h, ui.h]
2017-05-18 Fix compiler flags and warnings for libsurvive code.
    [main.cpp]
2017-05-19 Documented current robot, and add top-level Makefile with "make all" and "make clean".
2017-05-19 Update encoder wiring to 2017 version (reconstructed from firmware numbers).
2017-05-20 Document actual pins written on encoder motors, and update firmware to use "encoder_bus_2[3]" for pin 3, bus 2.
2017-05-20 Derp, fix bus on limit switches.
    [firmware.ino]
2017-05-20 2017 robot updates: no hooks so remove Mcount, no hardware bucket sensor so simulate it.
2017-05-20 Fixed kinect cm / meters confusion so it actually shows driveable areas.
    [display.h, main.cpp]
2017-05-20 Update robot display UI, so it shows the box raise position, and doesn't show battery voltage.
    [display.h]
2017-05-20 Read vive robot.tf in backend, and update robot location and pitch from it.
2017-05-23 Replace 278 with 268, and replace Rmax with the single box_raise_max.
    [main.cpp, robot.h]
2017-05-25 Updated firmware power limit to 255 (from 100) for drive motors, and updated drive rpm to 12 (from 6). This about doubles the speed.
2017-05-26 Override limit switches in torque control
2017-10-15 Add cad for new printed mining head.
    [barbie_gearbox.scad, drive_sprocket.scad]
2018-02-24 Added "kidmode" header file. This disables the dangerous joystick buttons.
2018-04-13 Added male drive train sprocket.
    [drive_sprocket_male.scad, drive_sprocket_retainer.scad, sprocketlib2D.scad]
2018-04-13 Added crowned version of drive sprocket.
    [one_piece_drive_crowned.scad]
2018-04-13 Added scissor spring version of track skis. This is the final version for FRONTIER.
    [track_skis.scad]
2018-05-07 Added scoop sides cad
    [scoopsi.scad]
2019-02-04 Add head_extend power to old robot, so new (2019) backend can drive it successfully.
2019-04-13 Added power limits to kidmoe.
